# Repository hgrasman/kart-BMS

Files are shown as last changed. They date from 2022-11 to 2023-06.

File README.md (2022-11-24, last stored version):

# BMS

## Getting started

To make it easy for you to get started with GitLab, here's a list of recommended next steps.

Already a pro? Just edit this README.md and make it your own. Want to make it easy? [Use the template at the bottom](#editing-this-readme)!

## Add your files

- [ ] [Create](https://docs.gitlab.com/ee/user/project/repository/web_editor.html#create-a-file) or [upload](https://docs.gitlab.com/ee/user/project/repository/web_editor.html#upload-a-file) files
- [ ] [Add files using the command line](https://docs.gitlab.com/ee/gitlab-basics/add-file.html#add-a-file-using-the-command-line) or push an existing Git repository with the following command:

```
cd existing_repo
git remote add origin https://gitlab.com/ev-kartz/hardware/bms.git
git branch -M main
git push -uf origin main
```

## Integrate with your tools

- [ ] [Set up project integrations](https://gitlab.com/ev-kartz/hardware/bms/-/settings/integrations)

## Collaborate with your team

- [ ] [Invite team members and collaborators](https://docs.gitlab.com/ee/user/project/members/)
- [ ] [Create a new merge request](https://docs.gitlab.com/ee/user/project/merge_requests/creating_merge_requests.html)
- [ ] [Automatically close issues from merge requests](https://docs.gitlab.com/ee/user/project/issues/managing_issues.html#closing-issues-automatically)
- [ ] [Enable merge request approvals](https://docs.gitlab.com/ee/user/project/merge_requests/approvals/)
- [ ] [Automatically merge when pipeline succeeds](https://docs.gitlab.com/ee/user/project/merge_requests/merge_when_pipeline_succeeds.html)

## Test and Deploy

Use the built-in continuous integration in GitLab.

- [ ] [Get started with GitLab CI/CD](https://docs.gitlab.com/ee/ci/quick_start/index.html)
- [ ] [Analyze your code for known vulnerabilities with Static Application Security Testing(SAST)](https://docs.gitlab.com/ee/user/application_security/sast/)
- [ ] [Deploy to Kubernetes, Amazon EC2, or Amazon ECS using Auto Deploy](https://docs.gitlab.com/ee/topics/autodevops/requirements.html)
- [ ] [Use pull-based deployments for improved Kubernetes management](https://docs.gitlab.com/ee/user/clusters/agent/)
- [ ] [Set up protected environments](https://docs.gitlab.com/ee/ci/environments/protected_environments.html)

***

# Editing this README

When you're ready to make this README your own, just edit this file and use the handy template below (or feel free to structure it however you want - this is just a starting point!). Thank you to [makeareadme.com](https://www.makeareadme.com/) for this template.

## Suggestions for a good README
Every project is different, so consider which of these sections apply to yours. The sections used in the template are suggestions for most open source projects. Also keep in mind that while a README can be too long and detailed, too long is better than too short. If you think your README is too long, consider utilizing another form of documentation rather than cutting out information.

## Name
Choose a self-explaining name for your project.

## Description
Let people know what your project can do specifically. Provide context and add a link to any reference visitors might be unfamiliar with. A list of Features or a Background subsection can also be added here. If there are alternatives to your project, this is a good place to list differentiating factors.

## Badges
On some READMEs, you may see small images that convey metadata, such as whether or not all the tests are passing for the project. You can use Shields to add some to your README. Many services also have instructions for adding a badge.

## Visuals
Depending on what you are making, it can be a good idea to include screenshots or even a video (you'll frequently see GIFs rather than actual videos). Tools like ttygif can help, but check out Asciinema for a more sophisticated method.

## Installation
Within a particular ecosystem, there may be a common way of installing things, such as using Yarn, NuGet, or Homebrew. However, consider the possibility that whoever is reading your README is a novice and would like more guidance. Listing specific steps helps remove ambiguity and gets people to using your project as quickly as possible. If it only runs in a specific context like a particular programming language version or operating system or has dependencies that have to be installed manually, also add a Requirements subsection.

## Usage
Use examples liberally, and show the expected output if you can. It's helpful to have inline the smallest example of usage that you can demonstrate, while providing links to more sophisticated examples if they are too long to reasonably include in the README.

## Support
Tell people where they can go to for help. It can be any combination of an issue tracker, a chat room, an email address, etc.

## Roadmap
If you have ideas for releases in the future, it is a good idea to list them in the README.

## Contributing
State if you are open to contributions and what your requirements are for accepting them.

For people who want to make changes to your project, it's helpful to have some documentation on how to get started. Perhaps there is a script that they should run or some environment variables that they need to set. Make these steps explicit. These instructions could also be useful to your future self.

You can also document commands to lint the code or run tests. These steps help to ensure high code quality and reduce the likelihood that the changes inadvertently break something. Having instructions for running tests is especially helpful if it requires external setup, such as starting a Selenium server for testing in a browser.

## Authors and acknowledgment
Show your appreciation to those who have contributed to the project.

## License
For open source projects, say how it is licensed.

## Project status
If you have run out of energy or time for your project, put a note at the top of the README saying that development has slowed down or stopped completely. Someone may choose to fork your project or volunteer to step in as a maintainer or owner, allowing your project to keep going. You can also make an explicit request for maintainers.

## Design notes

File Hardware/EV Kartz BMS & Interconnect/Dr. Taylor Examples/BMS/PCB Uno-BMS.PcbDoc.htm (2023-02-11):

Reporting Options

# File in Previous Format

Date | : | 12/1/2022
Time | : | 7:33:51 PM
Filename | : | C:\Users\Public\Documents\Altium\Projects\EV Kartz BMS & Interconnect\Dr. Taylor Examples\BMS\PCB Uno-BMS.PcbDoc

Version | Warning
Release 12 | CAUTION - Air Gap Width previously controlled by Clearance rule is now controlled by Polygon Connect Style rule's newly introduced Air Gap Width (set to default value). Suggest reviewing each Polygon Connect Style rule's Air Gap Width attribute for correctness.
Release 13 | CAUTION - Silkscreen Over Component Pads Rules are converted to Silk To Solder Mask Clearance Rules. Suggest examining rule scopes for accuracy.

This file was generated by an earlier version of the software

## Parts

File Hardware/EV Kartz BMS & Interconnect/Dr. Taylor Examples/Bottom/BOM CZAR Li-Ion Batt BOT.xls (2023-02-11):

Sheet: BOM Report
Bill of Materials |  |  | Bill of Materials For Project [CZAR Li-Ion Batt BOT.PrjPcb] (No PCB Document Selected)
Source Data From: |  | CZAR Li-Ion Batt BOT.PrjPcb |  |  |  | Creation Date: | 11/23/2022 | 6:29:14 PM
Project: |  | CZAR Li-Ion Batt BOT.PrjPcb |  |  |  | Print Date: | 2022-11-23 | 18:30:44
Variant: |  | None |  |  |  | Author: | <Parameter Author not found> |  |  |  | Production Quantity: |  | 2
Designator | #Column Name Error:Value | Footprint | Comment | #Column Name Error:Rated | #Column Name Error:Tol | Description | Supplier 1 | Supplier Part Number 1 | Supplier Unit Price 1 | Quantity | Per Unit | Supplier Order Qty 1 | Supplier Subtotal 1 | Category | 1 | 5 | 10 | 25 | 50 | 100 | 250 | 500 | 1000
JH11, JH12, JH13, JH14, JH15, JH16, JH17, JH18, JH31, JH32, JH33, JH34, JH35, JH36, JH37, JH38, JH51, JH52, JH53, JH54, JH55, JH56, JH57, JH58, JH71, JH72, JH73, JH74, JH75, JH76, JH77, JH78, JH91, JH92, JH93, JH94, JH95, JH96, JH97, JH98, JHB1, JHB2, JHB3, JHB4, JHB5, JHB6, JHB7, JHB8, JL21, JL22, JL23, JL24, JL25, JL26, JL27, JL28, JL41, JL42, JL43, JL44, JL45, JL46, JL47, JL48, JL61, JL62, JL63, JL64, JL65, JL66, JL67, JL68, JL81, JL82, JL83, JL84, JL85, JL86, JL87, JL88, JLA1, JLA2, JLA3, JLA4, JLA5, JLA6, JLA7, JLA8, JLC1, JLC2, JLC3, JLC4, JLC5, JLC6, JLC7, JLC8 |  | BAT-KS5202-PTH | 5202 |  |  | Hardware, Battery Contact Spring, PCB-mount | Digi-Key | 36-5202-ND | $0.28 | 96 | $26.52 | 192 | 53.05 | J | 0.32000 | 0.32000 | 0.32000 | 0.28240 | 0.28240 | 0.27630 | 0.25920 | 0.23070 | 0.23070
J1, J2, J3, J4, J5, J6, J7, J8 |  | JST-XH-B6 | B6B-XH-A(LF)(SN) |  |  | Header, JST, 6-Pin, Straight | Digi-Key | 455-2271-ND | $0.24 | 8 | $1.90 | 16 | 3.81 | J | 0.28000 | 0.28000 | 0.23800 | 0.23800 | 0.23800 | 0.18530 | 0.18530 | 0.15882 | 0.15882
 |  |  |  |  |  |  |  |  |  | 104 | $28.43 | 208 | 56.86
Approved |  | Notes
Capacitor Cost: | $0.000 | C
Diode Cost: | $0.000 | D
Fuse Cost: | $0.000 | F
Hardware Cost: | $0.000 | H
Connector Cost: | $28.429 | J
Inductor Cost: | $0.000 | L
MOSFET Cost: | $0.000 | M
Transistor Cost: | $0.000 | Q
Resistor Cost: | $0.000 | R
Transformer Cost: | $0.000 | T
ASIC Cost: | $0.000 | U

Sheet: Project Information
Project Full Path | D:\Dropbox\!Projects\CZAR Power\Li-Ion Batt\BotBrd\CZAR Li-Ion Batt BOT.PrjPcb
Project Filename | CZAR Li-Ion Batt BOT.PrjPcb
Variant Name | None
Data-Source Filename | CZAR Li-Ion Batt BOT.PrjPcb
Data-Source Full Path | D:\Dropbox\!Projects\CZAR Power\Li-Ion Batt\BotBrd\CZAR Li-Ion Batt BOT.PrjPcb
Title | Bill of Materials For Project [CZAR Li-Ion Batt BOT.PrjPcb] (No PCB Document Selected)
Total Quantity | 104
Report Time | 6:29:14 PM
Report Date | 11/23/2022
Report Date & Tine | 11/23/2022 6:29:14 PM
Output Name | Bill of Materials
Output Type | BOM_PartType
Output Generator Name | BOM
Output Generator Description | Bill of Materials

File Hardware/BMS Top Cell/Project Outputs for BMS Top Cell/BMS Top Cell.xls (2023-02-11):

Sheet: BOM Report
Bill of Materials |  |  | Bill of Materials for PCB Document [Top_Cell.PcbDoc]
Source Data From: |  | Top_Cell.PcbDoc |  |  |  | Creation Date: | 2/11/2023 | 14:45
Project: |  | BMS Top Cell.PrjPcb |  |  |  | Print Date: | 2023-02-11 | 14:45:48
Variant: |  | None |  |  |  | Author: | <Parameter Author not found> |  |  |  | Production Quantity: |  | 1
Designator | Value | Footprint | Comment | Rated | Tol | Description | Supplier 1 | Supplier Part Number 1 | Supplier Unit Price 1 | Quantity | Per Unit | Supplier Order Qty 1 | Supplier Subtotal 1 | Category
C100, C101, C102, C103 | 10µF | CAPC3225N | C1210C106K3RACAUTO | 25V | 10% | Capacitor, Ceramic, 10µF, 25V, 0805, 10%, 125C | Digi-Key | 399-7046-1-ND | $0.65 | 4 | $2.60 | 4 | $2.60 | C
J1, J2, J3, J4, J5, J6, J7, J8, J9, J10, J11, J12, J13, J14, J15, J16, J17, J18, J19, J20, J21, J22 |  | 6mm Pad | 2036-3-57-15-00-00-03-0 |  |  | Hardware, Sprint Contact Surface | Digi-Key | 54-2036-3-57-15-00-00-03-0CT-ND | $0.78 | 22 | $17.07 | 22 | $17.07
J48V, JFUSE |  | S98979 | S98979 |  |  | Screw Terminal M8, 360A | Digi-Key | 2101-S98979-ND | $4.30 | 2 | $8.60 | 2 | $8.60
JIN, JOUT |  | JST-PH-S7 | S7B-PH-SM4-TB(LF)(SN) |  |  | Header, JST, 7-Pin, Right-Angle, PH, Surface Mount | Digi-Key | 455-1754-1-ND | $0.89 | 2 | $1.78 | 2 | $1.78 | J
R100, R101, R102, R103 | 100k | RESC2012N | ERJ-6ENF1003V | 1/8W | 1% | Resistor, Fixed, 100 kOhm, 0805, 1%, 1/8W | Digi-Key | P100KCCT-ND | $0.10 | 4 | $0.40 | 4 | $0.40 | R
R104, R105, R106, R107 | 10 | RESC2012N | ERJ-6ENF10R0V | 1/8W | 1% | Resistor, Fixed, 10 Ohm, 0805, 1%, 1/8W | Digi-Key | P10.0CCT-ND | $0.10 | 4 | $0.40 | 4 | $0.40 | R
 |  |  |  |  |  |  |  |  |  | 38 | $30.85 | 38 | $30.85
Approved |  | Notes
Capacitor Cost: | $2.600 | C
Diode Cost: | $0.000 | D
Fuse Cost: | $0.000 | F
Hardware Cost: | $0.000 | H
Connector Cost: | $1.780 | J
Inductor Cost: | $0.000 | L
MOSFET Cost: | $0.000 | M
Transistor Cost: | $0.000 | Q
Resistor Cost: | $0.800 | R
Transformer Cost: | $0.000 | T
ASIC Cost: | $0.000 | U

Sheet: Project Information
Project Full Path | C:\Users\pcguy\Desktop\GitLab\BMS\bms\Hardware\BMS Top Cell\BMS Top Cell.PrjPcb
Project Filename | BMS Top Cell.PrjPcb
Variant Name | None
Data-Source Filename | Top_Cell.PcbDoc
Data-Source Full Path | C:\Users\pcguy\Desktop\GitLab\BMS\bms\Hardware\BMS Top Cell\Top_Cell.PcbDoc
Title | Bill of Materials for PCB Document [Top_Cell.PcbDoc]
Total Quantity | 38
Report Time | 14:45
Report Date | 2/11/2023
Report Date & Tine | 2/11/2023 14:45
Output Name | Bill of Materials
Output Type | BomReport
Output Generator Name | BOM
Output Generator Description | Bill of Materials

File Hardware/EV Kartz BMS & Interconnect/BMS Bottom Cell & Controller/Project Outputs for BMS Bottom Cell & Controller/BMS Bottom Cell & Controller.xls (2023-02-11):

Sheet: BOM Report
Bill of Materials |  |  | Bill of Materials for PCB Document [Bottom_Cell.PcbDoc]
Source Data From: |  | Bottom_Cell.PcbDoc |  |  |  | Creation Date: | 2/11/2023 | 2:56 PM
Project: |  | BMS Bottom Cell & Controller.PrjPcb |  |  |  | Print Date: | 2023-02-11 | 14:56:14
Variant: |  | None |  |  |  | Author: | <Parameter Author not found> |  |  |  | Production Quantity: |  | 1
Designator | Value | Footprint | Comment | Rated | Tol | Description | Supplier 1 | Supplier Part Number 1 | Supplier Unit Price 1 | Quantity | Per Unit | Supplier Order Qty 1 | Supplier Subtotal 1 | Category
C100, C101, C104 | 1µF | CAPC2012N | C0805C105K3RAC7210 | 25V | 10% | Capacitor, Ceramic, 1µF, 25V, 0805, 10%, 125C | Digi-Key | 399-C0805C105K3RAC7210CT-ND | $0.13 | 3 | $0.39 | 3 | $0.39 | C
C102, C103, C105, C108, C109, C200, C201, C202, C203, C204, C205, C304, C307, C316 | 100nF | CAPC2012N | C0805C104K1RACAUTO | 100V | 10% | Capacitor, Ceramic, 100nF, 100V, 0805, 10%, 125C | Digi-Key | 399-6926-1-ND | $0.19 | 14 | $2.66 | 14 | $2.66 | C
C106, C107, C401 | 10µF | CAPC3225N | C1210C106K3RACAUTO | 25V | 10% | Capacitor, Ceramic, 10µF, 25V, 0805, 10%, 125C | Digi-Key | 399-7046-1-ND | $0.65 | 3 | $1.95 | 3 | $1.95 | C
C110, C309, C315, C400 | 10nF | CAPC2012N | C0805C103K1RAC7025 | 100V | 10% | Capacitor, Ceramic, 10nF, 100V, 0805, 10%, 125C | Digi-Key | 399-C0805C103K1RAC7025CT-ND | $0.10 | 4 | $0.40 | 4 | $0.40 | C
C300, C306 | 1 µF, [NoValue] | CAP 0805_2012 | =Value |  |  | CAP CER 1UF 100V X7S 0805 | Digi-Key | 490-14464-1-ND | $0.37 | 2 | $0.74 | 2 | $0.74
C301, C302, C303, C310, C312, C_ISO100 | 10 µF, [NoValue], 100 pF | CAP 1206_3216 - 0.8MM | =Value |  |  | CAP CER 10UF 25V X5R 1206, CAP CER 100PF 1KV C0G/NP0 1206 | Digi-Key | 1292-1206X106K250CT-ND, 1276-3199-1-ND | $0.49 | 6 | $2.94 | 6 | $2.94
C305, C308, C311, C313, C402, C404, C405 | 100nF | CAPC2012N | CL21B104KACNNNC | 100V | 10% | Capacitor, Ceramic, 100nF, 25V, 0805, 10%, 125C | Digi-Key | 1276-1099-1-ND | $0.10 | 7 | $0.70 | 7 | $0.70 | C
C314, C403, C406 | 1nF | CAPC2012N | C0805C102K1RACAUTO | 100V | 10% | Capacitor, Ceramic, 1nF, 100V, 0805, 10%, 125C | Digi-Key | 399-6919-1-ND | $0.19 | 3 | $0.57 | 3 | $0.57 | C
CAN100 |  | 618009211721 | 618009211721 |  |  | Male PCB Connector without Hex Screw WR-DSUB, 8.08 mm, Angled, 9 pins | Farnell | 2827767 | $3.06 | 1 | $3.06 | 1 | $3.06
D100 | GRN | DIO2012N-G | LTST-C170GKT | 2.1V, 10mA, 6mcd |  | LED, SMT 0805, Green, 2.1V, 10mA | Digi-Key | 160-1179-1-ND | $0.30 | 1 | $0.30 | 1 | $0.30 | D
D200 | RED | DIO2012N-R | LTST-C170KRKT | 2.0V, 20mA, 54mcd |  | LED, SMT 0805, Red, 2.0V, 20mA | Digi-Key | 160-1415-1-ND | $0.31 | 1 | $0.31 | 1 | $0.31 | D
D300, D301 |  | DIODES SOT-523 | =Part Number |  |  | DIODE ZENER 3.3V 150MW SOT523 | Digi-Key | MMBZ5226BTDICT-ND | $0.41 | 2 | $0.82 | 2 | $0.82
D400, D401 | 850mV @ 2A | SOD123 | SMD210PL-TP | 2A, 100V |  | Diode, Si Sch, 100V, 2A, SOD123 | Digi-Key | SMD210PL-TPMSCT-ND | $0.40 | 2 | $0.80 | 2 | $0.80 | D
F400 | 12mOhm | CAPC1608N | 0440005.WR | 5A, 32V |  | Fuse, SMT, 5A, 32VAC/VDC, 1206 | Digi-Key | F1608CT-ND | $1.09 | 1 | $1.09 | 1 | $1.09 | F
IC400, IC401 |  | DIODES SOT-23-3 | =Part Number |  |  | MOSFET N-CH 30V 4A SOT23 | Digi-Key | DMG3418L-7DICT-ND | $0.43 | 2 | $0.86 | 2 | $0.86
J200, J201, J202, J203, J204, J205, J206, J207, J208, J209, J210, J211, J212, J213, J214, J215, J216, J217, J218, J219, J220, J221 |  | 6mm Pad | 2036-3-57-15-00-00-03-0 |  |  | Hardware, Sprint Contact Surface | Digi-Key | 54-2036-3-57-15-00-00-03-0CT-ND | $0.78 | 22 | $17.07 | 22 | $17.07
J400, J_LEM300, J_Relay400 | 4 Pos | 22041041 | 22041041 | N/A | N/A | Header, 4 pos, 2.5mm pitch, Molex Kit Parts Housing: 0511910400 Terminals: 0508028000 | Digi-Key | WM18787-ND | $0.98 | 3 | $2.94 | 3 | $2.94 | J
JOUT400 |  | JST-PH-S7 | S7B-PH-SM4-TB(LF)(SN) |  |  | Header, JST, 7-Pin, Right-Angle, PH, Surface Mount | Digi-Key | 455-1754-1-ND | $0.89 | 1 | $0.89 | 1 | $0.89 | J
JPOS200 |  | S98979 | S98979 |  |  | Screw Terminal M8, 360A |  |  |  | 1 | $0.00
JPROG100 |  | HDR1X5 SMT | 3-647167-5 |  |  | Header, 1x5-Pin, SMT, 100mil Pitch | Digi-Key | A144616-ND | $3.28 | 1 | $3.28 | 1 | $3.28 | J
L100 | 220@100MHz | INDC2012N | 742792022 | 2A |  | Inductor, 220 Ohms @ 100MHz, 2A, 50 mOhm, Ferrite Bead | Digi-Key | 732-1614-1-ND | $0.23 | 1 | $0.23 | 1 | $0.23 | L
L101 | 10uH | INDC3225N | BRL3225T100K | 700mA, 0.42 Ohm |  | Inductor, 10uH, 700mA, 420mOhm, Ferrite Bead | Digi-Key | 587-2167-1-ND | $0.25 | 1 | $0.25 | 1 | $0.25 | L
M200 | 30mOhm @ 10V | TO252-3N | AOD454A | 40V, 20A |  | MOSFET, N-Ch, 40V, 20A, 430mOhm, TO252 | Digi-Key | 785-1223-1-ND | $0.67 | 1 | $0.67 | 1 | $0.67 | M
R100, R301, R302, R303, R305, R306, R308 | 120 Ohms, 604 kOhms, 200 Ohms, 52.3 kOhms, 150 kOhms | RES 0805_2012 | =Value |  |  | RES 120 OHM 1% 1/8W 0805, RES 604K OHM 1% 1/8W 0805, RES 200 OHM 0.5% 1/8W 0805, RES 52.3K OHM 1% 1/8W 0805, RES 150K OHM 0.1% 1/8W 0805 | Digi-Key | 311-120CRCT-ND, 738-RMCF0805FT604KCT-ND, P123819CT-ND, RMCF0805FT52K3CT-ND, P150KDACT-ND | $0.10 | 7 | $0.70 | 7 | $0.70
R101, R104, R204, R208, R304, R307, R311, R412, R413 | 10k | RESC2012N | ERJ-6ENF1002V | 1/8W | 1% | Resistor, Fixed, 10 kOhm, 0805, 1%, 1/8W | Digi-Key | P10.0KCCT-ND | $0.10 | 9 | $0.90 | 9 | $0.90 | R
R102, R103, R300, R309, R317 | 1k | RESC2012N | ERJ-6ENF1001V | 1/8W | 1% | Resistor, Fixed, 1 kOhm, 0805, 1%, 1/8W | Digi-Key | P1.00KCCT-ND | $0.10 | 5 | $0.50 | 5 | $0.50 | R
R200 | 499k | RESC2012N | ERJ-6ENF4993V | 1/8W | 1% | Resistor, Fixed, 499 kOhm, 0805, 1%, 1/8W | Digi-Key | P499KCCT-ND | $0.10 | 1 | $0.10 | 1 | $0.10 | R
R201, R203, R205, R206 | 1 | RESC6432N | 35221R0JT | 3W | 5% | Resistor, Power, 1 Ohm, 6432, 5%, 3W | Digi-Key | A121177CT-ND | $0.76 | 4 | $3.04 | 4 | $3.04 | R
R202, R_ISO100 | 1Meg | RESC2012N | ERJ-6ENF1004V | 1/8W | 1% | Resistor, Fixed, 1 MOhm, 0805, 1%, 1/8W | Digi-Key | P1.00MCCT-ND | $0.10 | 2 | $0.20 | 2 | $0.20 | R
R207, R402, R403, R406, R407, R410, R411 | 10 | RESC2012N | ERJ-6ENF10R0V | 1/8W | 1% | Resistor, Fixed, 10 Ohm, 0805, 1%, 1/8W | Digi-Key | P10.0CCT-ND | $0.10 | 7 | $0.70 | 7 | $0.70 | R
R209, R210, R211, R212, R213, R310, R400, R401, R404, R405, R408, R409 | 100k | RESC2012N | ERJ-6ENF1003V | 1/8W | 1% | Resistor, Fixed, 100 kOhm, 0805, 1%, 1/8W | Digi-Key | P100KCCT-ND | $0.09 | 12 | $1.10 | 12 | $1.10 | R
R214, R215, R216, R217, R218 | 100k | RESC2012N | NT08105F4050B1F | 3570K | 1% | Resistor, NTC Thermistor, 100kOhm, 0805, 1%, 125C | Digi-Key | 283-NT08105F4050B1FCT-ND | $0.29 | 5 | $1.45 | 5 | $1.45 | R
R312 | 100 | RESC2012N | ERJ-6ENF1000V | 1/8W | 1% | Resistor, Fixed, 100 Ohm, 0805, 1%, 1/8W | Digi-Key | P100CCT-ND | $0.10 | 1 | $0.10 | 1 | $0.10 | R
R313, R314, R315 | 30k | RESC2012N | ERJ-6ENF3002V | 1/8W | 1% | Resistor, Fixed, 30 kOhm, 0805, 1%, 1/8W | Digi-Key | P30.0KCCT-ND | $0.10 | 3 | $0.30 | 3 | $0.30 | R
R316 | 20k | RESC2012N | ERJ-6ENF2002V | 1/8W | 1% | Resistor, Fixed, 20 kOhm, 0805, 1%, 1/8W | Digi-Key | P20.0KCCT-ND | $0.10 | 1 | $0.10 | 1 | $0.10 | R
U100 |  | DIODES INC SOT-89 | =Part Number |  |  | IC REG LINEAR 5V 150MA SOT89 | Digi-Key | AP7381-50Y-13DICT-ND | $0.38 | 1 | $0.38 | 1 | $0.38
U101 |  | SOIC-8-300 | ADM3050EBRIZ |  |  | IC, Transceiver, CAN FD, 0.5-6V, ISOLATED | Digi-Key | 505-ADM3050EBRIZ-ND | $6.01 | 1 | $6.01 | 1 | $6.01 | U
U102 |  | SAMC21 | ATSAMC21E18A-ANT |  |  | ARM Microcontrollers - MCU 32TQFP,105C TEMP, GREEN, 5V, 48MHZ | Mouser | 556-ATSAMC21E18A-ANT | $4.49 | 1 | $4.49 | 1 | $4.49
U300 |  | SOT23-5N | AZV331KTR-G1 | 2.2V~5.5V |  | Comparator, Single, Open-Drain, 84mA, 2.2V~5.5V | Digi-Key | AZV331KTR-G1DICT-ND | $0.45 | 1 | $0.45 | 1 | $0.45 | U
U301 |  | DHC | LTC3265HDHC#PBF |  |  | Supply, Bipolar Charge Pump, +/-15V | Mouser | 584-LTC3265HDHC#PBF | $12.48 | 1 | $12.48 | 1 | $12.48
U302, U_danger400, U_warn400 |  | TSSOP-8 | 74AHC2G00DP,125 | 5.5V, 24mA |  | Logic, NAND, Dual, Schmitt Trigger, TSSOP-8 | Digi-Key | 1727-6521-1-ND | $0.48 | 3 | $1.44 | 3 | $1.44 | U
U303 |  | TI SOT-23-5 DBV | =Part Number |  |  | IC OPAMP GP 1 CIRCUIT SOT23-5 | Digi-Key | LM321MFX/NOPBCT-ND | $0.64 | 1 | $0.64 | 1 | $0.64
U304 |  | SOT23-5N | LMV321SN3T1G | 2.7V~5.5V, 160mA |  | Op-Amp, Single, 1MHz, 1V/us, R2R, 2.7V~5.5V, 160mA | Digi-Key | LMV321SN3T1GOSCT-ND | $0.55 | 1 | $0.55 | 1 | $0.55 | U
U400 |  | SOT23-6N | SN74LVC1G11DBVR | 1.65 ~ 5.5V |  | Logic, AND, Single, 3-In, SOT23-6 | Digi-Key | 296-16810-1-ND | $0.41 | 1 | $0.41 | 1 | $0.41 | U
 |  |  |  |  |  |  |  |  |  | 151 | $78.96 | 150 | $78.96
Approved |  | Notes
Capacitor Cost: | $6.670 | C
Diode Cost: | $1.410 | D
Fuse Cost: | $1.090 | F
Hardware Cost: | $0.000 | H
Connector Cost: | $7.110 | J
Inductor Cost: | $0.480 | L
MOSFET Cost: | $0.670 | M
Transistor Cost: | $0.000 | Q
Resistor Cost: | $8.494 | R
Transformer Cost: | $0.000 | T
ASIC Cost: | $8.860 | U

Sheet: Project Information
Project Full Path | C:\Users\Jon\Dropbox\EV Kartz\EV Kartz BMS & Interconnect\BMS Bottom Cell & Controller\BMS Bottom Cell & Controller.PrjPcb
Project Filename | BMS Bottom Cell & Controller.PrjPcb
Variant Name | None
Data-Source Filename | Bottom_Cell.PcbDoc
Data-Source Full Path | C:\Users\Jon\Dropbox\EV Kartz\EV Kartz BMS & Interconnect\BMS Bottom Cell & Controller\Bottom_Cell.PcbDoc
Title | Bill of Materials for PCB Document [Bottom_Cell.PcbDoc]
Total Quantity | 151
Report Time | 2:56 PM
Report Date | 2/11/2023
Report Date & Tine | 2/11/2023 2:56 PM
Output Name | Bill of Materials
Output Type | BomReport
Output Generator Name | BOM
Output Generator Description | Bill of Materials

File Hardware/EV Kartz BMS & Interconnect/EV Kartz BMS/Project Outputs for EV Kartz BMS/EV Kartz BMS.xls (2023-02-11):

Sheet: BOM Report
Bill of Materials |  |  | Bill of Materials for PCB Document [reg_PCB.PcbDoc]
Source Data From: |  | reg_PCB.PcbDoc |  |  |  | Creation Date: | 2/11/2023 | 4:03 PM
Project: |  | EV Kartz BMS.PrjPcb |  |  |  | Print Date: | 2023-02-11 | 16:03:29
Variant: |  | None |  |  |  | Author: | <Parameter Author not found> |  |  |  | Production Quantity: |  | 1
Designator | Value | Footprint | Comment | Rated | Tol | Description | Supplier 1 | Supplier Part Number 1 | Supplier Unit Price 1 | Quantity | Per Unit | Supplier Order Qty 1 | Supplier Subtotal 1 | Category
C100, C101, C102, C103, C104 | 10µF | CAPC3225N | C1210C106K3RACAUTO | 25V | 10% | Capacitor, Ceramic, 10µF, 25V, 0805, 10%, 125C | Digi-Key | 399-7046-1-ND | $0.65 | 5 | $3.25 | 5 | $3.25 | C
C105, C106, C107, C108, C109, C110 | 100nF | CAPC2012N | C0805C104K1RACAUTO | 100V | 10% | Capacitor, Ceramic, 100nF, 100V, 0805, 10%, 125C | Digi-Key | 399-6926-1-ND | $0.28 | 6 | $1.68 | 6 | $1.68 | C
D100 | RED | DIO2012N-R | LTST-C170KRKT | 2.0V, 20mA, 54mcd |  | LED, SMT 0805, Red, 2.0V, 20mA | Digi-Key | 160-1415-1-ND | $0.31 | 1 | $0.31 | 1 | $0.31 | D
D101 | GRN | DIO2012N-G | LTST-C170GKT | 2.1V, 10mA, 6mcd |  | LED, SMT 0805, Green, 2.1V, 10mA | Digi-Key | 160-1179-1-ND | $0.30 | 1 | $0.30 | 1 | $0.30 | D
F1 | 12mOhm | CAPC1608N | 0440005.WR | 5A, 32V |  | Fuse, SMT, 5A, 32VAC/VDC, 1206 | Digi-Key | F1608CT-ND | $1.09 | 1 | $1.09 | 1 | $1.09 | F
J200_N, J200_P, J201_N, J201_P, J202_N, J202_P, J203_N, J203_P, J204_N, J204_P, J205_N, J205_P, J206_N, J206_P, J207_N, J207_P, J208_N, J208_P, J209_N, J209_P, J210_N, J210_P, J211_N, J211_P, J212_N, J212_P, J213_N, J213_P, J214_N, J214_P, J215_N, J215_P, J216_N, J216_P, J217_N, J217_P, J218_N, J218_P, J219_N, J219_P, J220_N, J220_P, J221_N, J221_P |  | 6mm Pad | 2036-3-57-15-00-00-03-0 |  |  | Hardware, Sprint Contact Surface | Digi-Key | 54-2036-3-57-15-00-00-03-0CT-ND | $0.74 | 44 | $32.75 | 44 | $32.75
JIN100, JOUT100 |  | JST-PH-S7 | S7B-PH-SM4-TB(LF)(SN) |  |  | Header, JST, 7-Pin, Right-Angle, PH, Surface Mount | Digi-Key | 455-1754-1-ND | $0.89 | 2 | $1.78 | 2 | $1.78 | J
JPROG100 |  | HDR1X5 SMT | 3-647167-5 |  |  | Header, 1x5-Pin, SMT, 100mil Pitch | Digi-Key | A144616-ND | $3.28 | 1 | $3.28 | 1 | $3.28 | J
M100 | 30mOhm @ 10V | TO252-3N | AOD454A | 40V, 20A |  | MOSFET, N-Ch, 40V, 20A, 430mOhm, TO252 | Digi-Key | 785-1223-1-ND | $0.67 | 1 | $0.67 | 1 | $0.67 | M
R100, R101, R102, R103, R108, R112, R113, R114, R115 | 100k | RESC2012N | ERJ-6ENF1003V | 1/8W | 1% | Resistor, Fixed, 100 kOhm, 0805, 1%, 1/8W | Digi-Key | P100KCCT-ND | $0.10 | 9 | $0.90 | 9 | $0.90 | R
R104, R105, R106, R107, R124 | 10 | RESC2012N | ERJ-6ENF10R0V | 1/8W | 1% | Resistor, Fixed, 10 Ohm, 0805, 1%, 1/8W | Digi-Key | P10.0CCT-ND | $0.10 | 5 | $0.50 | 5 | $0.50 | R
R109, R119, R120, R121, R122 | 100k | RESC2012N | NT08105F4050B1F | 3570K | 1% | Resistor, NTC Thermistor, 100kOhm, 0805, 1%, 125C | Digi-Key | 283-NT08105F4050B1FCT-ND | $0.29 | 5 | $1.45 | 5 | $1.45 | R
R110, R111, R118, R123 | 1 | RESC6432N | 35221R0JT | 3W | 5% | Resistor, Power, 1 Ohm, 6432, 5%, 3W | Digi-Key | A121177CT-ND | $0.76 | 4 | $3.04 | 4 | $3.04 | R
R116, R117, R127 | 10k | RESC2012N | ERJ-6ENF1002V | 1/8W | 1% | Resistor, Fixed, 10 kOhm, 0805, 1%, 1/8W | Digi-Key | P10.0KCCT-ND | $0.10 | 3 | $0.30 | 3 | $0.30 | R
R125 | 499k | RESC2012N | ERJ-6ENF4993V | 1/8W | 1% | Resistor, Fixed, 499 kOhm, 0805, 1%, 1/8W | Digi-Key | P499KCCT-ND | $0.10 | 1 | $0.10 | 1 | $0.10 | R
R126 | 1Meg | RESC2012N | ERJ-6ENF1004V | 1/8W | 1% | Resistor, Fixed, 1 MOhm, 0805, 1%, 1/8W | Digi-Key | P1.00MCCT-ND | $0.10 | 1 | $0.10 | 1 | $0.10 | R
U100 | 32MHz | SOIC-20-300 | PIC16F1508T-I/SO | 2.3V ~ 5.5V |  | MCU, 8-Bit, 5V, 32MHz, 20-Pin SOIC | Digi-Key | PIC16F1578-I/SS-ND | $1.37 | 1 | $1.37 | 1 | $1.37 | U
 |  |  |  |  |  |  |  |  |  | 91 | $52.87 | 91 | $52.87
Approved |  | Notes
Capacitor Cost: | $4.930 | C
Diode Cost: | $0.610 | D
Fuse Cost: | $1.090 | F
Hardware Cost: | $0.000 | H
Connector Cost: | $5.060 | J
Inductor Cost: | $0.000 | L
MOSFET Cost: | $0.670 | M
Transistor Cost: | $0.000 | Q
Resistor Cost: | $6.390 | R
Transformer Cost: | $0.000 | T
ASIC Cost: | $1.370 | U

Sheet: Project Information
Project Full Path | C:\Users\Jon\Dropbox\EV Kartz\EV Kartz BMS & Interconnect\EV Kartz BMS\EV Kartz BMS.PrjPcb
Project Filename | EV Kartz BMS.PrjPcb
Variant Name | None
Data-Source Filename | reg_PCB.PcbDoc
Data-Source Full Path | C:\Users\Jon\Dropbox\EV Kartz\EV Kartz BMS & Interconnect\EV Kartz BMS\reg_PCB.PcbDoc
Title | Bill of Materials for PCB Document [reg_PCB.PcbDoc]
Total Quantity | 91
Report Time | 4:03 PM
Report Date | 2/11/2023
Report Date & Tine | 2/11/2023 4:03 PM
Output Name | Bill of Materials
Output Type | BomReport
Output Generator Name | BOM
Output Generator Description | Bill of Materials

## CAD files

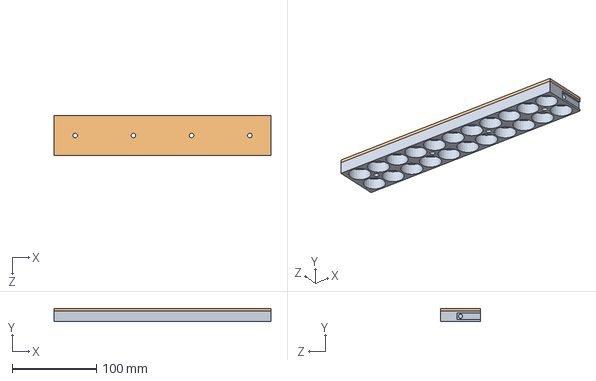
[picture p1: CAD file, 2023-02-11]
Hardware/EV Kartz BMS & Interconnect/EV Kartz BMS/Mechanical/21700_Battery_Pack_Dec20_2022/1_wide_cap_pcb_subassm.SLDASM
257.2 x 15.0 x 47.4 mm
Cap_21700_single
end_pcb

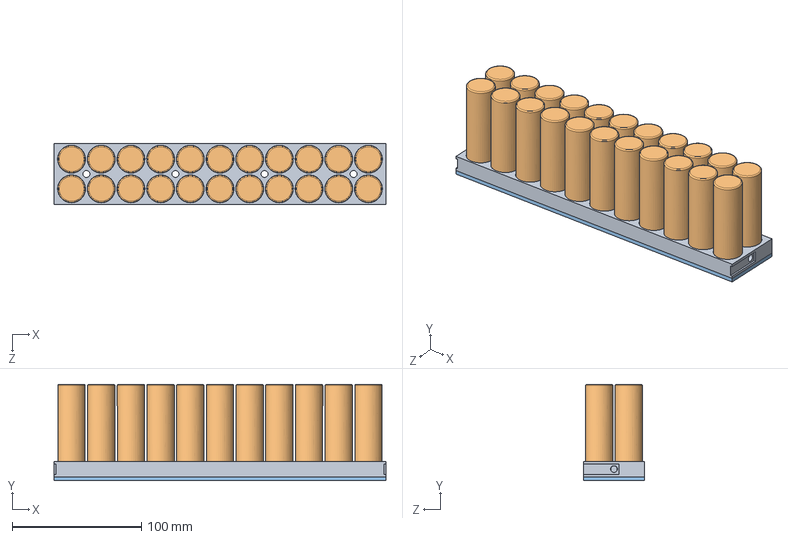
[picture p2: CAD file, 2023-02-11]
Hardware/EV Kartz BMS & Interconnect/EV Kartz BMS/Mechanical/21700_Battery_Pack_Dec20_2022/1_wide_subassm_neg.SLDASM
257.2 x 74.7 x 47.4 mm
Cap_21700_single
21700_Cell x 22
end_pcb

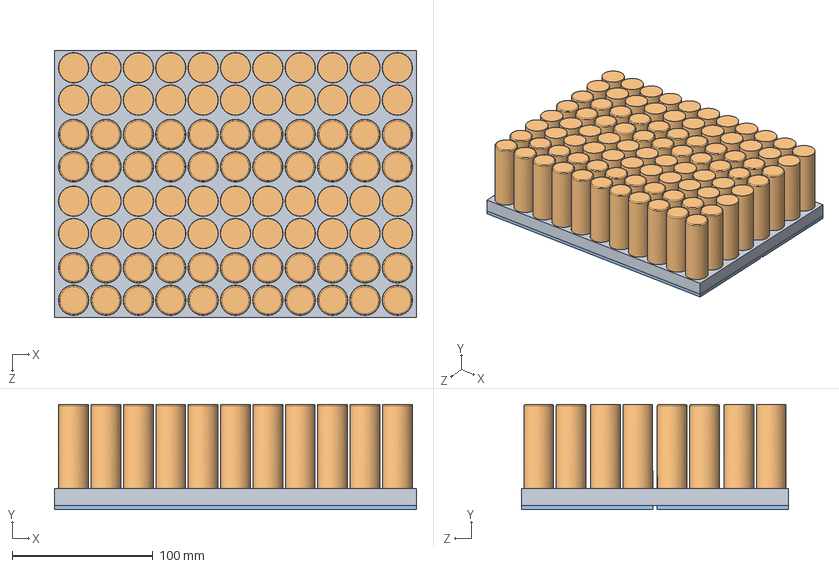
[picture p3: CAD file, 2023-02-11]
Hardware/EV Kartz BMS & Interconnect/EV Kartz BMS/Mechanical/21700_Battery_Pack_Dec20_2022/4_wide_subassm.SLDASM
257.2 x 74.7 x 189.6 mm
Cap_21700_double
21700_Cell x 88
4_wide_pcb x 2

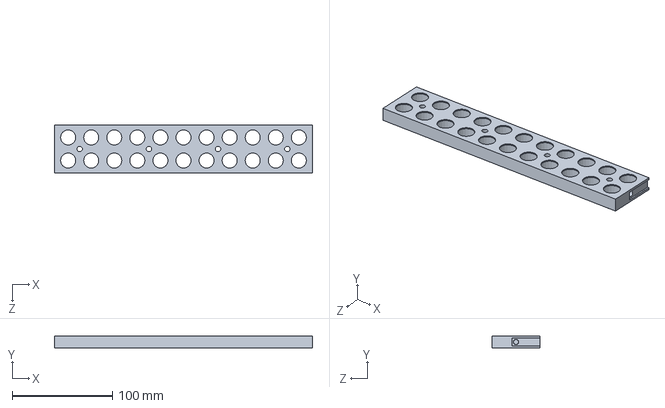
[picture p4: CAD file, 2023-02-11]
Hardware/EV Kartz BMS & Interconnect/EV Kartz BMS/Mechanical/21700_Battery_Pack_Dec20_2022/single_cap_w_pcb.SLDASM
257.2 x 12.0 x 47.4 mm

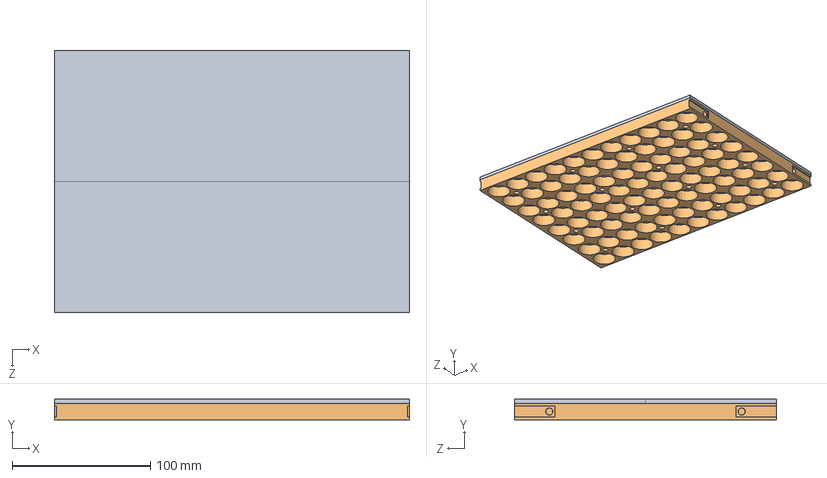
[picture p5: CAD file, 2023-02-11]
Hardware/EV Kartz BMS & Interconnect/EV Kartz BMS/Mechanical/21700_Battery_Pack_Dec20_2022/4_wide_cap_pcb_subassm.SLDASM
257.2 x 15.0 x 189.6 mm
4_wide_pcb x 2
Cap_21700_double

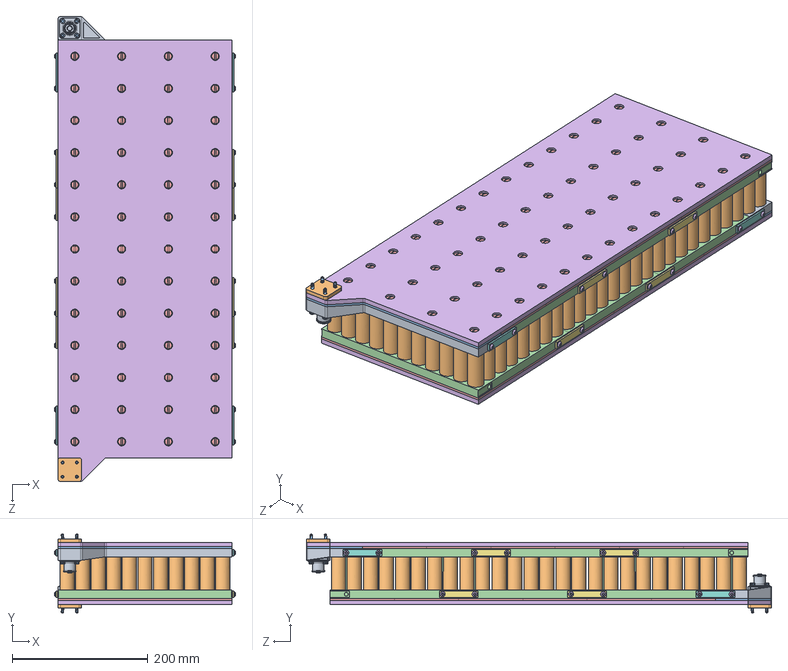
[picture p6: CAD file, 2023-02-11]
Hardware/EV Kartz BMS & Interconnect/EV Kartz BMS/Mechanical/21700_Battery_Pack_Dec20_2022/Assem_21700_Full_Pack.SLDASM
267.6 x 116.1 x 686.2 mm
Cap_21700_single x 2
21700_Cell x 286
end_pcb x 2
Cap_21700_double x 6
4_wide_pcb x 12
Clear_Cover x 2
Tie_Bar x 8
Tie_Bar_Short x 4
Surlok Plus 200A SLPRBTPSO x 2
91290A184_Black-Oxide Alloy Steel Socket Head Screw x 8
93121A375_6063_rod x 52
93121A375_6063_bolt x 52
92095A189_Button Head Hex Drive Screw x 24

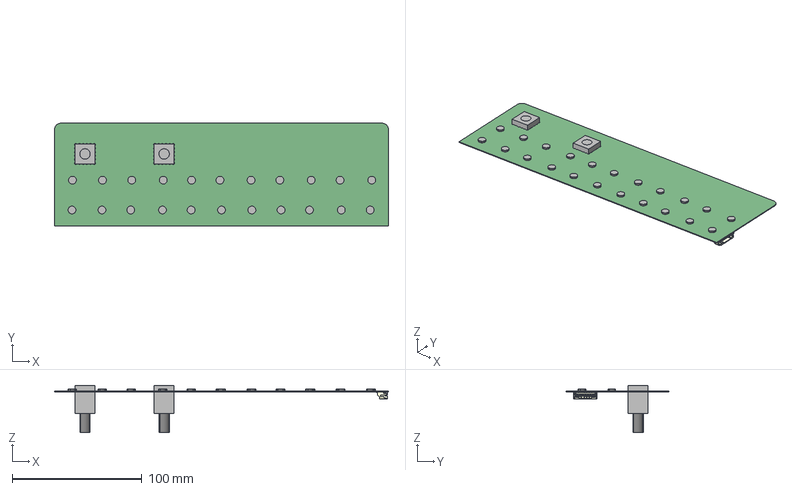
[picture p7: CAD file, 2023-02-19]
Hardware/BMS Top Cell/Project Outputs for BMS Top Cell/Top_Cell.step
257.2 x 79.1 x 36.5 mm
S7B-PH-SM4-TB-LF
Extruded x 26

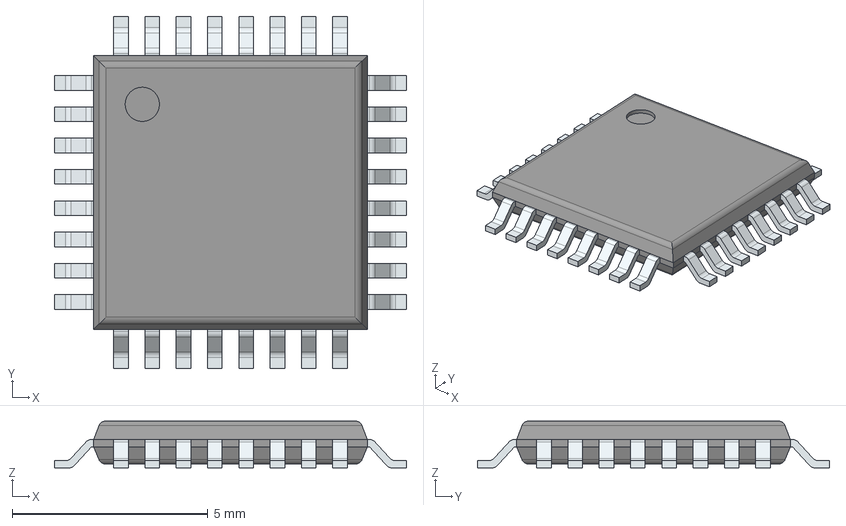
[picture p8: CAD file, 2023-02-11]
Hardware/EV Kartz BMS & Interconnect/BMS Bottom Cell & Controller/Mechanical/ATSAMC21E18A-ANT.stp
9.00 x 9.00 x 1.20 mm
PinsArrayLR
PinsArrayTB

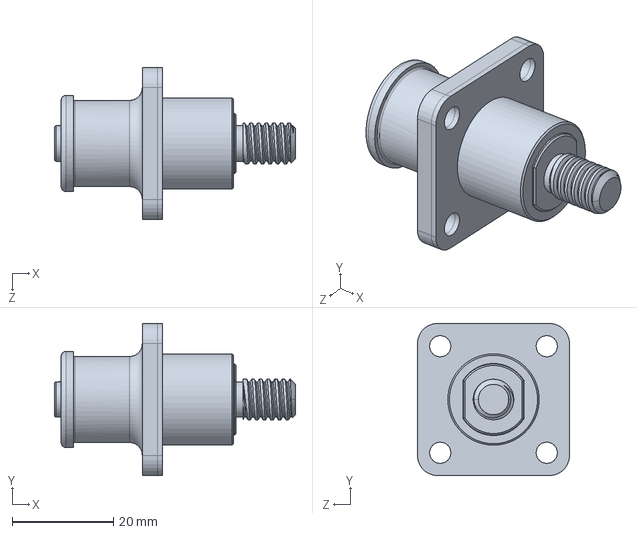
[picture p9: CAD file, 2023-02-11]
Hardware/EV Kartz BMS & Interconnect/EV Kartz BMS/Mechanical/21700_Battery_Pack_Dec20_2022/amphenol-surlok-plus-slprbtpso-1.snapshot.1/Surlok Plus 200A SLPRBTPSO.SLDPRT
47.5 x 30.0 x 30.0 mm

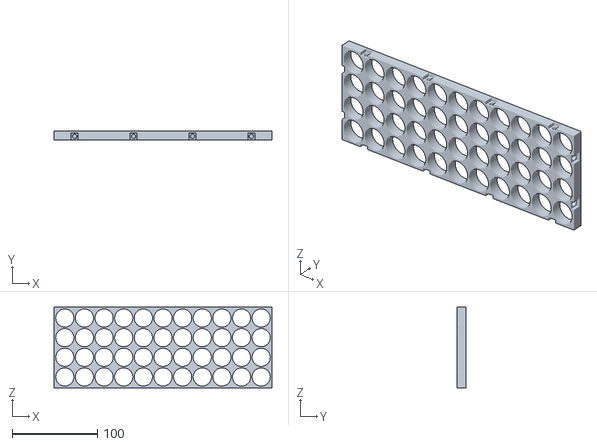
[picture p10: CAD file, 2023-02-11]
Hardware/EV Kartz BMS & Interconnect/EV Kartz BMS/Mechanical/21700_Battery_Pack_Dec20_2022/Test1/Cap_21700.STL
255.3 x 10.0 x 94.3

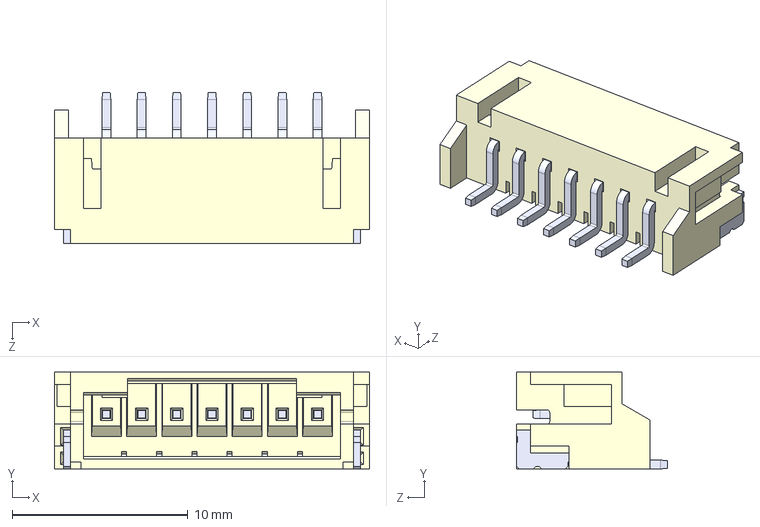
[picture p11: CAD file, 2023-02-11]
Hardware/EV Kartz BMS & Interconnect/EV Kartz BMS/Mechanical/S7B-PH-SM4-TB-LF.STEP
17.9 x 5.50 x 8.60 mm

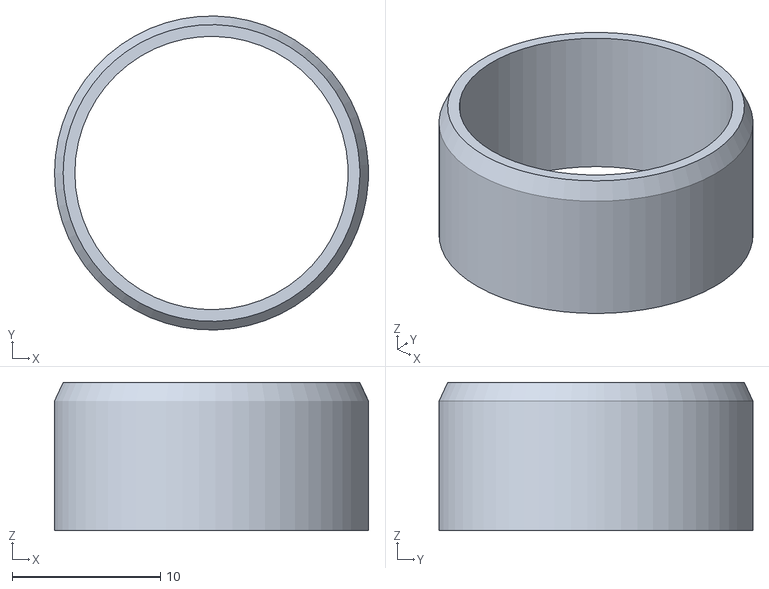
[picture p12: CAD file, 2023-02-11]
Hardware/EV Kartz BMS & Interconnect/EV Kartz BMS/Mechanical/21700_Battery_Pack_Dec20_2022/Test1/Spacer_Test1.STL
21.2 x 21.2 x 10.0

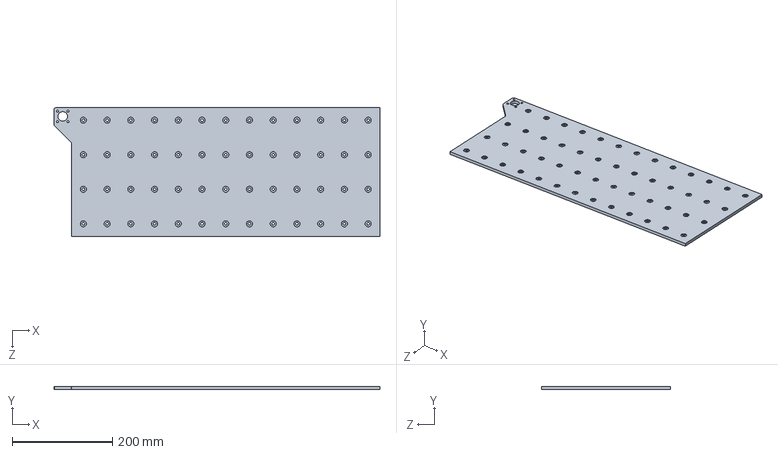
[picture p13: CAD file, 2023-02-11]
Hardware/EV Kartz BMS & Interconnect/EV Kartz BMS/Mechanical/21700_Battery_Pack_Dec20_2022/Clear_Cover.SLDPRT
651.2 x 6.35 x 257.2 mm

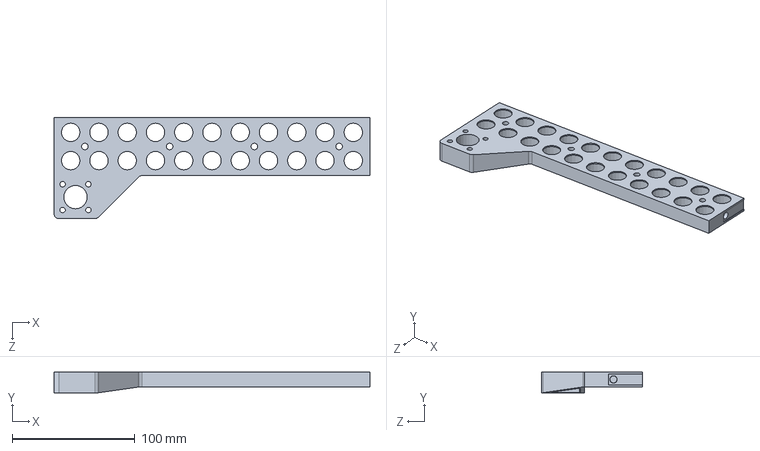
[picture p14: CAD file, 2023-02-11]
Hardware/EV Kartz BMS & Interconnect/EV Kartz BMS/Mechanical/21700_Battery_Pack_Dec20_2022/Cap_21700_single.SLDPRT
257.2 x 17.0 x 82.4 mm

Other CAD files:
Hardware/EV Kartz BMS & Interconnect/EV Kartz BMS/Mechanical/21700_Battery_Pack_Dec20_2022/1_wide_subassm_pos.SLDASM
Hardware/EV Kartz BMS & Interconnect/EV Kartz BMS/Mechanical/21700_Battery_Pack_Dec20_2022/1_wide_subassm.SLDASM
Hardware/EV Kartz BMS & Interconnect/EV Kartz BMS/Mechanical/21700_Battery_Pack_Dec20_2022/Cap_21700_single_a.SLDPRT
Hardware/EV Kartz BMS & Interconnect/EV Kartz BMS/Mechanical/21700_Battery_Pack_Dec20_2022/Tie_Bar.SLDPRT
Hardware/EV Kartz BMS & Interconnect/EV Kartz BMS/Mechanical/21700_Battery_Pack_Dec20_2022/21700_Cell.SLDPRT
Hardware/EV Kartz BMS & Interconnect/EV Kartz BMS/Mechanical/21700_Battery_Pack_Dec20_2022/21700_clearance_Test1.SLDPRT
Hardware/EV Kartz BMS & Interconnect/EV Kartz BMS/Mechanical/21700_Battery_Pack_Dec20_2022/4_wide_pcb.SLDPRT
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

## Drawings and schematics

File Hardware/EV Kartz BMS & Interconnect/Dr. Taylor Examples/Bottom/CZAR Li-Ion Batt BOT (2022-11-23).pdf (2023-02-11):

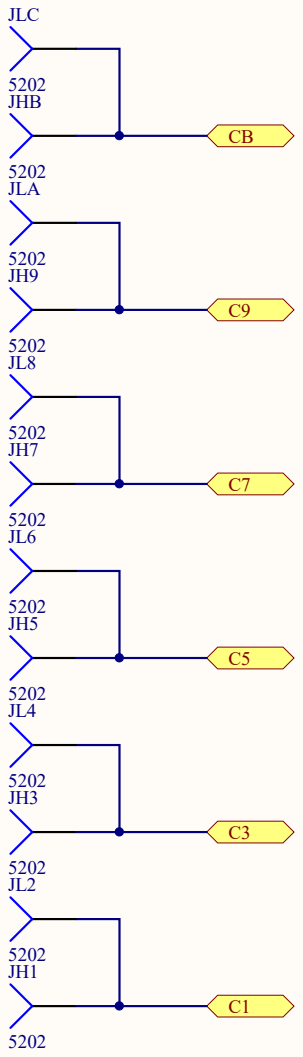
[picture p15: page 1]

CZAR Power - Li-Ion Batt Brd BOT Title | Adv Power Electronics Lab Kettering University 1700 University Ave Flint, MI 48504 United States of America

Size: Letter | Number: 2 | Revision:

Date: 11/23/2022 Time: 6:27:16 PM | | Sheet 2 of 7

D:\Dropbox\!Projects\CZAR Power\Li-Ion Batt\BotBrd\SCH Pg2 Cell Bank.SchDoc

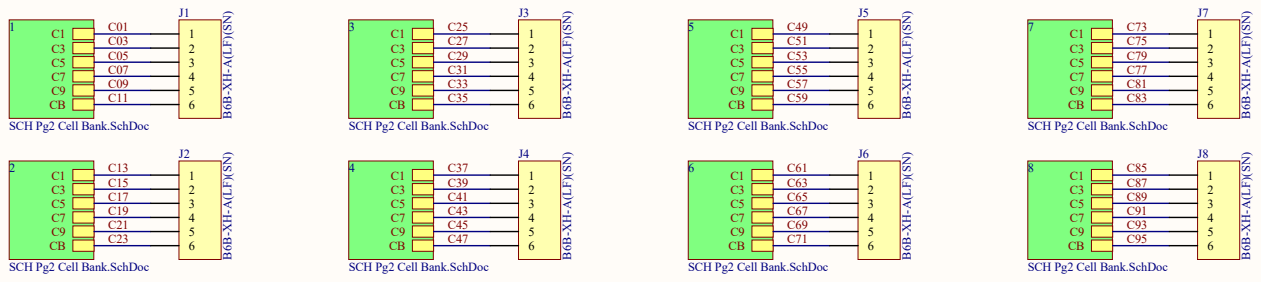
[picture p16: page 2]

CZA R Power - Li-Ion Batt Brd B O T | Adv Power Electronics Lab Kettering University 1700 University Av e Flint, MI 48504 United States of America

Letter | 2 | Re v ision:

11/23/2022 Time: 6:27:16 PM | | Sheet 2 of 7

AR Power\Li-Ion Batt\BotBrd\SCH Pg1 Top Sheet.SchDoc

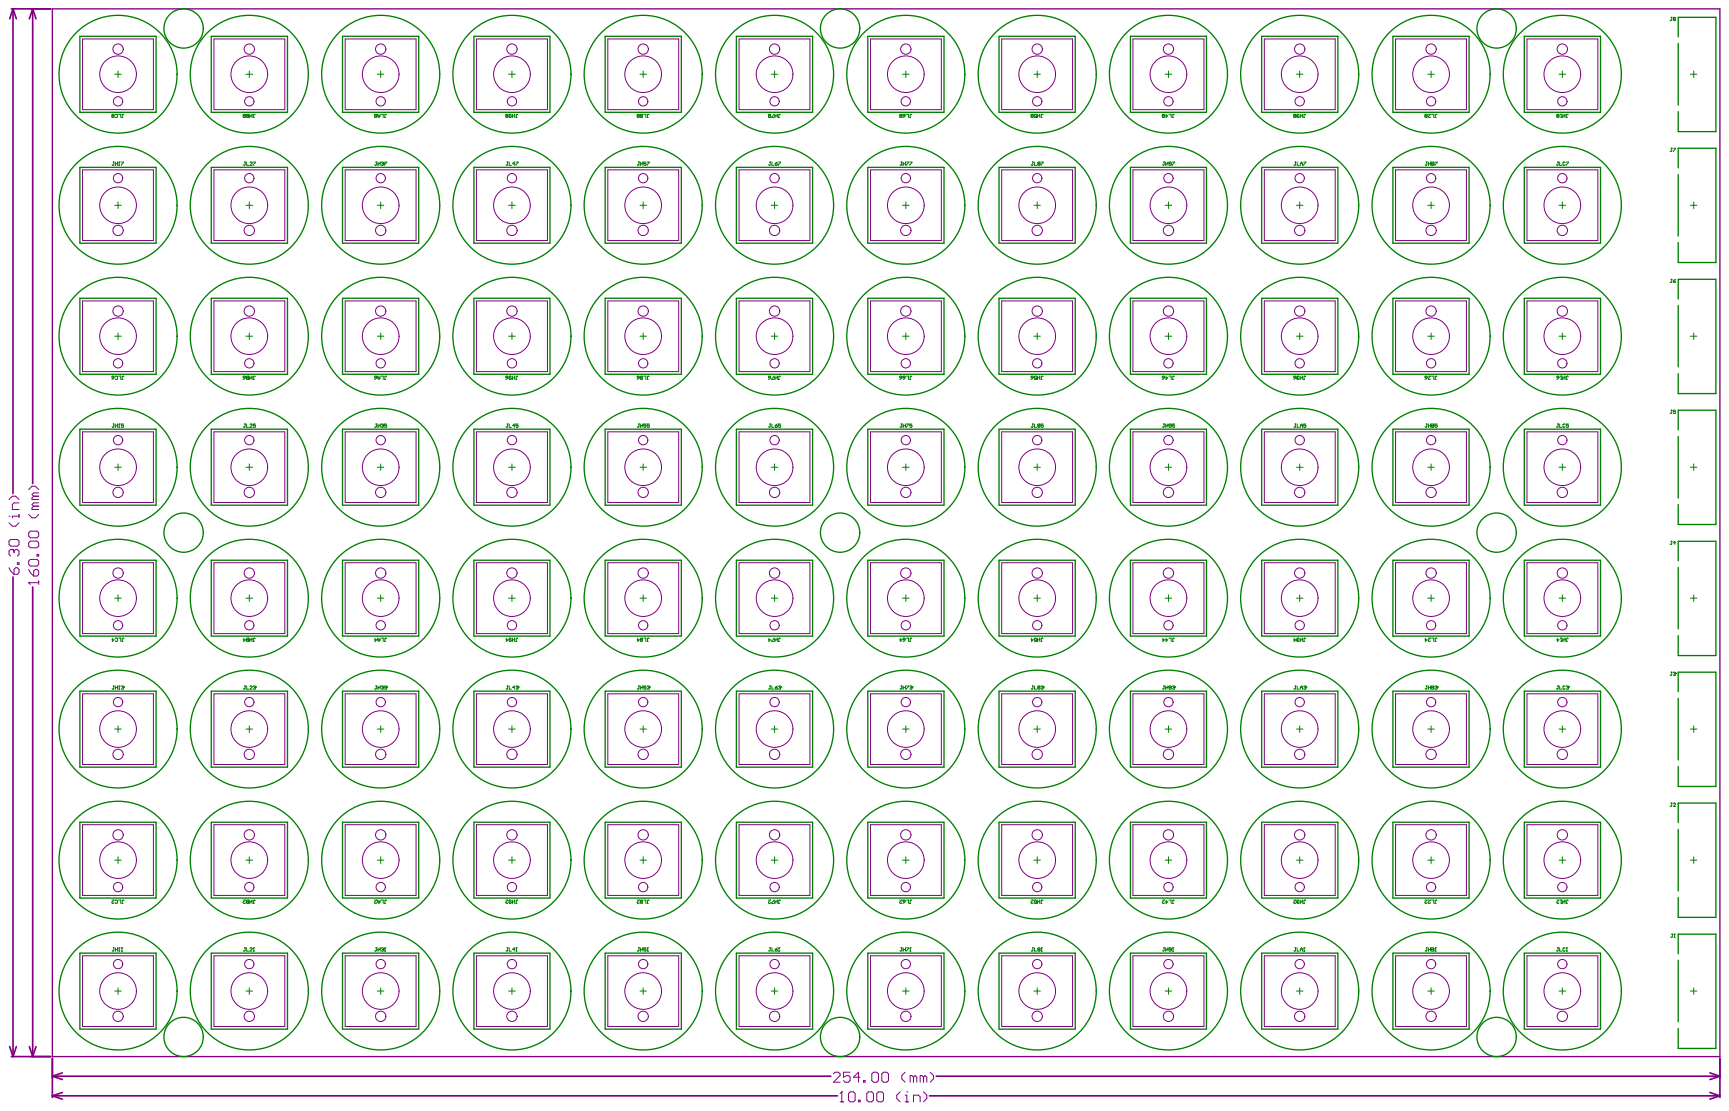
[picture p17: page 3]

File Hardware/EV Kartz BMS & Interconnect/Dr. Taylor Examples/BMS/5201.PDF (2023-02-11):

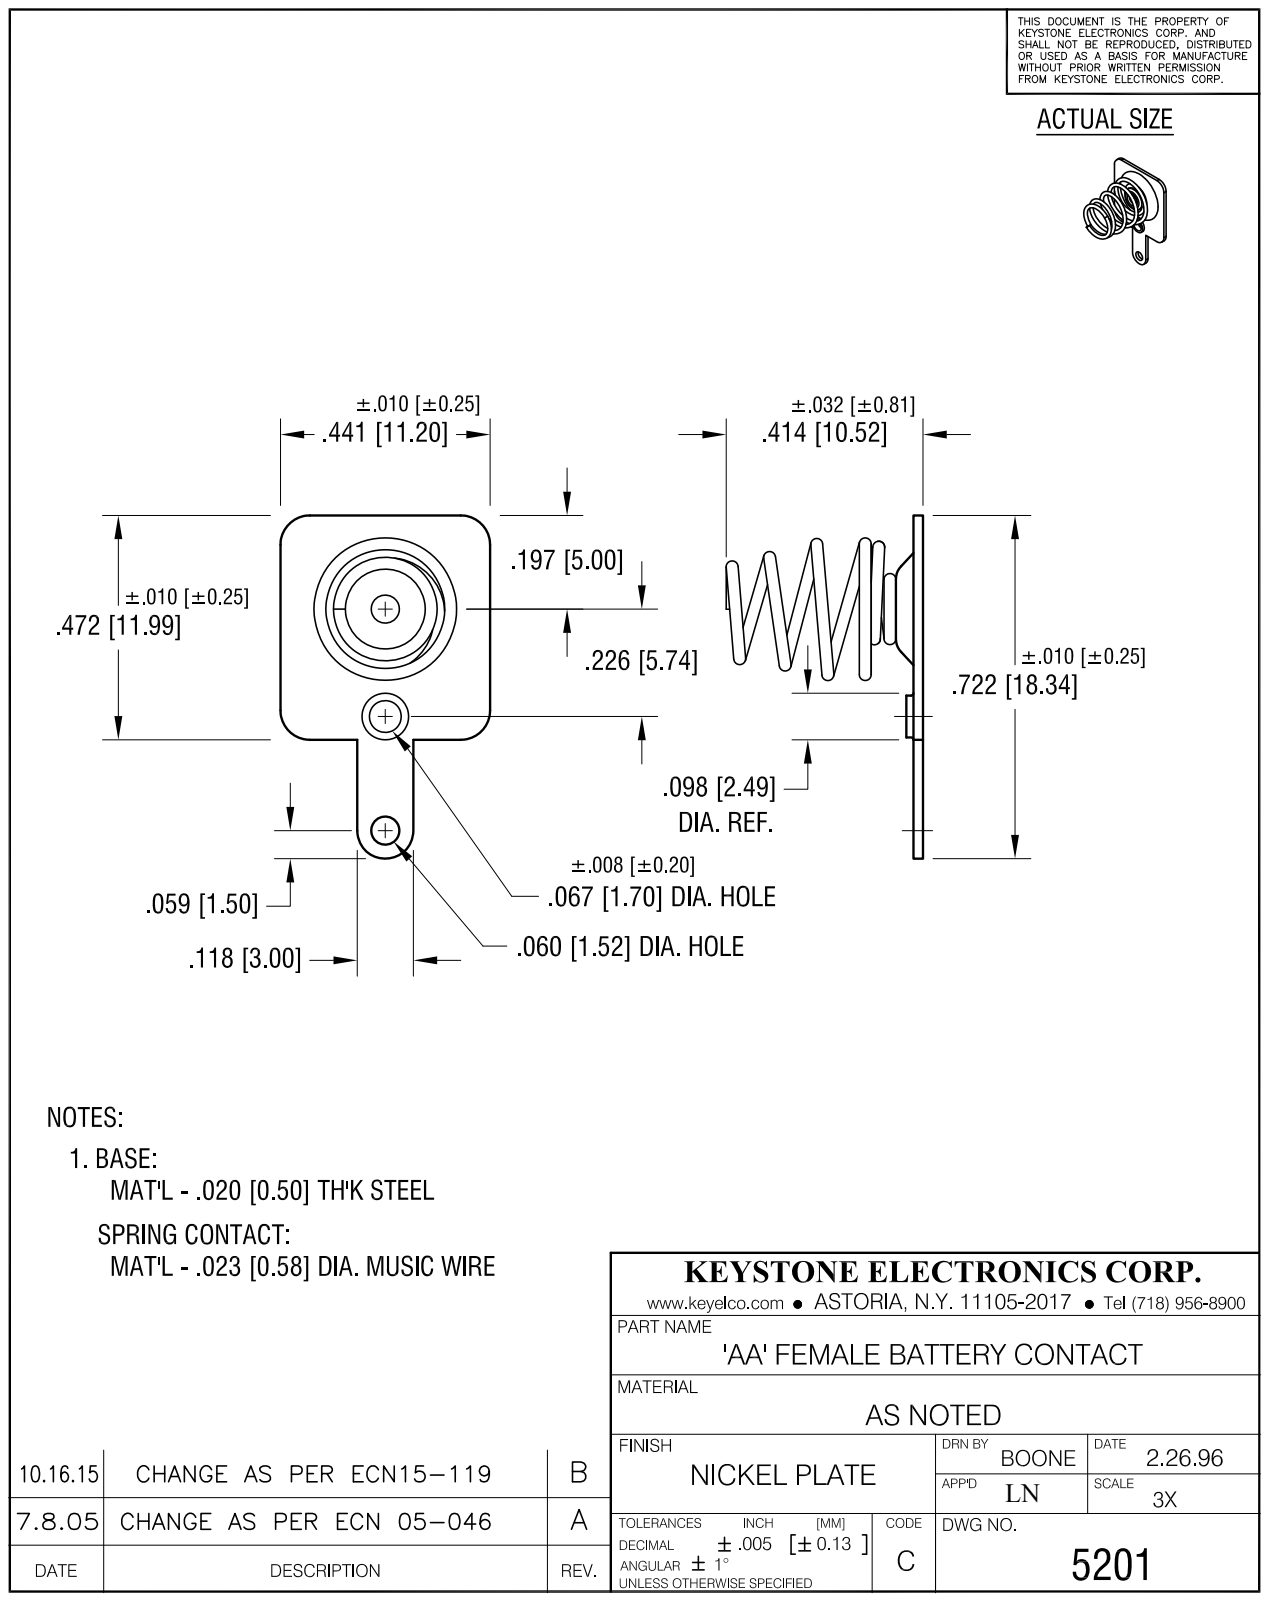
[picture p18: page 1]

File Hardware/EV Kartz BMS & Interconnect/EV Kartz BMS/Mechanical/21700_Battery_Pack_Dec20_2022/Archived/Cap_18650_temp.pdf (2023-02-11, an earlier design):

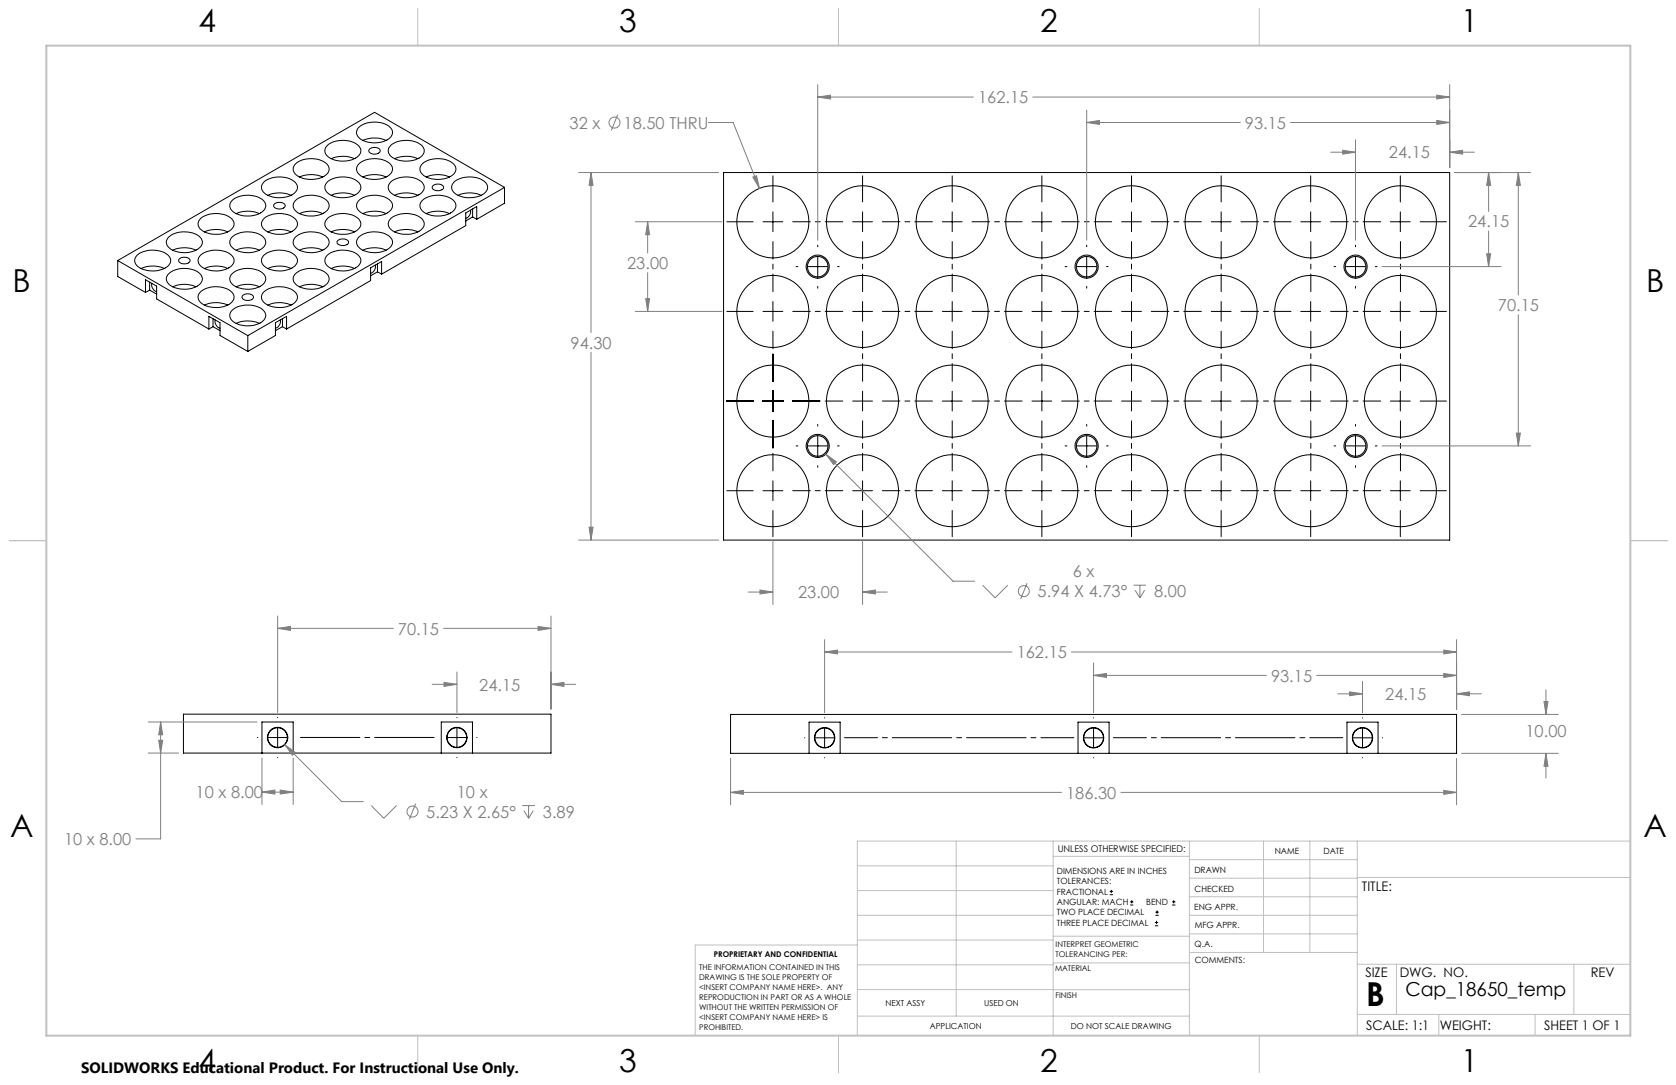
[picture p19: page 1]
32 x 18.50 THRU

UNLESS OTHERWISE SPECIFIED: | | NAME | DATE
DIMENSIONS ARE IN INCHES TOLERANCES: FRACTIONAL ANGULAR: MACH BEND TWO PLACE DECIMAL THREE PLACE DECIMAL | DRAWN

CHECKED | | | TITLE:

ENG APPR.
MFG APPR.

INTERPRET GEOMETRIC TOLERANCING PER: | Q.A.
MATERIAL | | SIZE B | DWG. NO. Cap_18650_temp | REV

PROPRIETARY AND CONFIDENTIAL
THE INFORMATION CONTAINED IN THIS
DRAWING IS THE SOLE PROPERTY OF
<INSERT COMPANY NAME HERE>. ANY
REPRODUCTION IN PART OR AS A WHOLE
WITHOUT THE WRITTEN PERMISSION OF
<INSERT COMPANY NAME HERE> IS
PROHIBITED.

NEXT ASSY | USED ON | FINISH

APPLICATION | DO NOT SCALE DRAWING | | SCALE: 1:1 | WEIGHT: | SHEET 1 OF 1

SOLIDWORKS Educational Product. For Instructional Use Only.

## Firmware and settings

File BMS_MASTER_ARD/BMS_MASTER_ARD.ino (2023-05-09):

#include <Wire.h>

#define SAM_VSENSE_PIN A5
#define SAM_BAL_PIN 5
#define SAM_T1_PIN A3
#define SAM_T2_PIN A4
#define SAM_RELAY_PIN 8
#define SAM_SSTART_PIN 10
#define SAM_CURR_PIN A2
#define SAM_CHARGE_SWITCH_PIN 7

inline void slowStartRelay(){ //  
  digitalWrite(SAM_SSTART_PIN, HIGH); //precharge for 4.5 seconds
  delay(900);
  digitalWrite(SAM_RELAY_PIN, HIGH); //close main relay
  delay(100);
  digitalWrite(SAM_SSTART_PIN, LOW); //disconnect precharge relay after additional .5s
}
inline void stopRelay(){ // 
  digitalWrite(SAM_RELAY_PIN, LOW); //cut relay
  digitalWrite(SAM_SSTART_PIN, LOW); //redundant just in case
}


unsigned long lastRead;
double current;
double charge = 0;

void setup() {

  // Setup I2C and uart
  Wire.begin();
  Serial.begin(115200);
  Wire.setWireTimeout(5000, true);

  //setup balance command 
  pinMode(SAM_BAL_PIN, OUTPUT);
  digitalWrite(SAM_BAL_PIN, LOW); //balance init off

  //setup Relay pins
  pinMode(SAM_RELAY_PIN, OUTPUT);
  pinMode(SAM_SSTART_PIN, OUTPUT);
  digitalWrite(SAM_RELAY_PIN, LOW);
  digitalWrite(SAM_SSTART_PIN, LOW);

  //setup charge/discharge switch pin
  pinMode(SAM_CHARGE_SWITCH_PIN, INPUT_PULLUP);
      
  lastRead = millis();
}

#define MINADDR 8
#define MAXADDR 19
#define CONTROLVOLT 0x11
#define ARRADDR addr-MINADDR
#define NUMTEMPS 5
#define BALANCETHRESH 0

#define CURRENT_MAX_ALLOWED 350 

#define MINV 3.2
#define MINV_LOADED 2.8
#define MAXV 4.2
#define MAXTEMP 60

#define LEM_CENTER_OFFSET 1.485
#define LEM_RANGE 3.0
#define CURRENTMAX 400

double avgs[MAXADDR - MINADDR + 1];
bool balnce[MAXADDR - MINADDR + 1];
double temps[MAXADDR - MINADDR + 1][NUMTEMPS];
bool sam_balance;
double sam_volt;
double sam_temp1;
double sam_temp2;
bool chargeMode;
bool relayClosed = false;

void loop() {
  // put your main code here, to run repeatedly:

  union booga{
    uint8_t raw[2];
    uint16_t mashed;
  }booling;  

  chargeMode = digitalRead(SAM_CHARGE_SWITCH_PIN); //poll switch for pack mode

  double rel_avg = 0;
  uint8_t count = 0;
  double min_v = 5;
  double max_v = 0;
  double max_temp = 0;
  for (int addr = MINADDR; addr <= MAXADDR; addr++ ){
    //Serial.print("Polling:"); Serial.println(addr);

    Wire.beginTransmission(addr);
    Wire.write(CONTROLVOLT | balnce[ARRADDR]<<5);
    byte error = Wire.endTransmission(); // run transaction
    delay(6);

    if (error){
      //Serial.println("NACK");
      avgs[ARRADDR] = -1;
    }else{
      Wire.requestFrom(addr, 2);
      booling.raw[0] = Wire.read();
      booling.raw[1] = Wire.read();
      if (avgs[ARRADDR]>0){ avgs[ARRADDR] = (double) (.85*(double)avgs[ARRADDR] + .15*(double)booling.mashed);} //convert to volts
      else{avgs[ARRADDR] = (double)booling.mashed;} //lost contact, get value
      double volts = (2.048 * 1024) / avgs[ARRADDR];
      Serial.print("Found: "); Serial.print(addr); Serial.print(" Counts: "); Serial.print(avgs[ARRADDR]); Serial.print(" VOLTS: "); Serial.println(volts);
      rel_avg += volts; count++;
      if (volts>max_v){max_v = volts;}
      if (volts<min_v){min_v = volts;}

      //get temp data
      for (int i = 0; i<NUMTEMPS; i++){
        Wire.beginTransmission(addr);
        Wire.write((uint8_t) i+1 | balnce[ARRADDR]<<5);
        byte error = Wire.endTransmission(); // run transaction
        delay(6);

        if (error){
          //Serial.println("NACK");
          temps[ARRADDR][i] = -1;
        }else{
          Wire.requestFrom(addr, 2);
          booling.raw[0] = Wire.read();
          booling.raw[1] = Wire.read();      
        }
        if (temps[ARRADDR][i]>0){ temps[ARRADDR][i] = (double) (.5*(double)temps[ARRADDR][i] + .5*(double)booling.mashed);} //convert to volts
        else{temps[ARRADDR][i] = (double)booling.mashed;} //lost contact, get value
        double temp_OHMS = -(100000*temps[ARRADDR][i]) / (temps[ARRADDR][i] - 1024);
        double temp_actual = 55.31 * exp((temp_OHMS/1000)*-0.07449) + 63.29*exp((temp_OHMS/1000)*-0.009305);
        if (temp_actual < 500){
          if (temp_actual>max_temp){max_temp = temp_actual;}
        }
        Serial.print(" T"); Serial.print(i+1); Serial.print(": "); Serial.print(temp_actual);
        delay(3);
      }   
      Serial.println();       
    }
    delay(3);  

  }

  digitalWrite(SAM_BAL_PIN, LOW); //stop balancing
  delay(80); //necessary for voltage to stabilize
  sam_volt = .5*sam_volt + .5*(double) analogRead(SAM_VSENSE_PIN); //include samc
  double sam_volt_actual = (sam_volt*5 ) / 1024;
  if (sam_volt_actual>max_v){max_v = sam_volt_actual;}
  if (sam_volt_actual<min_v){min_v = sam_volt_actual;}
  sam_temp1 = .5*sam_temp1 + .5*(double) analogRead(SAM_T1_PIN);
  sam_temp2 = .5*sam_temp2 + .5*(double) analogRead(SAM_T2_PIN);
  double sam_t1_OHMS = -(100000*sam_temp1) / (sam_temp1 - sam_volt); //scales temp reading to pack voltage
  double sam_t2_OHMS = -(100000*sam_temp2) / (sam_temp2 - sam_volt); //because thermistors are not referenced to 5v
  double sam_T1_actual = 55.31 * exp((sam_t1_OHMS/1000)*-0.07449) + 63.29*exp((sam_t1_OHMS/1000)*-0.009305);
  double sam_T2_actual = 55.31 * exp((sam_t2_OHMS/1000)*-0.07449) + 63.29*exp((sam_t2_OHMS/1000)*-0.009305);
  Serial.print("NEG: Volt: "); Serial.print(sam_volt_actual); Serial.print(" T1: "); Serial.print(sam_T1_actual); Serial.print(" T2: "); Serial.println(sam_T2_actual); 

  //calculate avg voltages
  if (count>1){
    rel_avg += sam_volt_actual; //include samc
    Serial.print("Count: "); Serial.print(count); Serial.print(" TOT: "); Serial.println(rel_avg);
    rel_avg = rel_avg/(count+1);
  }else if (count==1){
    rel_avg = rel_avg;
  }else{
    Serial.println("Zero Count");
    rel_avg = -1;
  }

  //decide balancing
  for (int addr = MINADDR; addr <= MAXADDR; addr++ ){
    if (avgs[ARRADDR]<0){continue;}   
    if (rel_avg<0){break;} 
    double volts = (2.048 * 1024) / avgs[ARRADDR];
    if (chargeMode && ((volts - rel_avg) > BALANCETHRESH)){ //flag for balance during charge only
      balnce[ARRADDR] = true;
      Serial.print("Balancing: "); Serial.println(addr);
    }else{
      balnce[ARRADDR] = false;
    }  
  }

  if (rel_avg>0){
    if (chargeMode && ((sam_volt_actual - rel_avg) > BALANCETHRESH)){
      digitalWrite(SAM_BAL_PIN, HIGH);
      Serial.println("Balancing SAM");
    }
  }

  Serial.print("MIN: "); Serial.print(min_v);  Serial.print(" AVG: "); Serial.print(rel_avg); Serial.print(" MAX: "); Serial.println(max_v);
  Serial.print("MAX TEMP: "); Serial.println(max_temp);

  //current sensing
  double lem_volts = ((double)analogRead(SAM_CURR_PIN)*5)/1024;
  current = (1 * ((double) ((lem_volts - LEM_CENTER_OFFSET)/(LEM_RANGE/2)) * CURRENTMAX)) + ((double) (7 + 7 * (lem_volts-LEM_CENTER_OFFSET))); //Current
  charge += current*(double)(lastRead-millis()) /1000; //charge count
  lastRead = millis();
  Serial.print("LEM Volts: "); Serial.print(lem_volts); Serial.print("Current: "); Serial.print(current); Serial.print(" Charge: "); Serial.println(charge);


  //determine if relay should be closed/open
  if (chargeMode && relayClosed){ 
    stopRelay(); //open relay
    relayClosed = false;
    Serial.println("RELAY OPEN: CHARGE READY");
  }
  if (!chargeMode && !relayClosed){ //need to discharge but relay is open
    if (min_v > MINV){ //close if above min cell voltage
      slowStartRelay(); //close relay
      relayClosed = true;
      Serial.println("RELAY CLOSED: DISCHARGE READY");
    }else{Serial.println("CANNOT CLOSE RELAY: VOLTAGE LOW");}
  }

  // enforce safety limits
  if (chargeMode){
    if (max_v >= MAXV){stopRelay(); relayClosed = false; Serial.println("RELAY TRIP MAX V");} //too high disconnect charger
  }else{
    if (min_v <= MINV_LOADED){stopRelay(); relayClosed = false; Serial.println("RELAY TRIP MIN V");} //enforce minimum loaded
  }
  if (current > CURRENT_MAX_ALLOWED){
    stopRelay();
    Serial.println("OVERCURRENT: TIMEOUT 1s");
    delay(1000);
  }
  if (max_temp>MAXTEMP){
    stopRelay();
    Serial.println("OVERTEMP: TIMEOUT 1s");
    delay(1000);
  }
  if (count == 0) {
    stopRelay();
    Serial.println("Cell Lost: TIMEOUT 1s");
    delay(1000);
  } 
  
}

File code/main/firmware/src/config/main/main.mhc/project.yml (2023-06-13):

files:
- generatedChecksum: E4894B6355AF41AED546E4C6C20005C1
  logicalPath: FreeRTOS/Source
  name: FreeRTOS_tasks.c
  physicalPath: ../../third_party/rtos/FreeRTOS/Source
  security: NON_SECURE
  type: SOURCE
  userChecksum: E4894B6355AF41AED546E4C6C20005C1
- generatedChecksum: null
  logicalPath: ''
  name: average.c
  physicalPath: ../..
  security: NON_SECURE
  type: SOURCE
  userChecksum: null
- generatedChecksum: null
  logicalPath: ''
  name: can.c
  physicalPath: ../..
  security: NON_SECURE
  type: SOURCE
  userChecksum: null
- generatedChecksum: null
  logicalPath: ''
  name: checks.c
  physicalPath: ../..
  security: NON_SECURE
  type: SOURCE
  userChecksum: null
- generatedChecksum: 4490B523D4D89767AF3FE31B825F7F6D
  logicalPath: FreeRTOS/Source
  name: croutine.c
  physicalPath: ../../third_party/rtos/FreeRTOS/Source
  security: NON_SECURE
  type: SOURCE
  userChecksum: 4490B523D4D89767AF3FE31B825F7F6D
- generatedChecksum: null
  logicalPath: ''
  name: current.c
  physicalPath: ../..
  security: NON_SECURE
  type: SOURCE
  userChecksum: null
- generatedChecksum: AE64199B660AA4499B58FCA9D9AD5792
  logicalPath: config/main/driver/i2c
  name: drv_i2c.c
  physicalPath: driver/i2c/src
  security: NON_SECURE
  type: SOURCE
  userChecksum: AE64199B660AA4499B58FCA9D9AD5792
- generatedChecksum: 37780F17759DED907A0F36E28BFB3136
  logicalPath: config/main/driver/i2c
  name: drv_i2c_local.h
  physicalPath: driver/i2c/src
  security: NON_SECURE
  type: SOURCE
  userChecksum: 37780F17759DED907A0F36E28BFB3136
- generatedChecksum: 0E0E8AECB67046FEA847B359ACE7A1F6
  logicalPath: FreeRTOS/Source
  name: event_groups.c
  physicalPath: ../../third_party/rtos/FreeRTOS/Source
  security: NON_SECURE
  type: SOURCE
  userChecksum: 0E0E8AECB67046FEA847B359ACE7A1F6
- generatedChecksum: 0D18A719A1E40A8875895284967F66D0
  logicalPath: config/main
  name: exceptions.c
  physicalPath: ''
  security: NON_SECURE
  type: SOURCE
  userChecksum: 0D18A719A1E40A8875895284967F66D0
- generatedChecksum: CF89BE92AE72229779903C2E9A760455
  logicalPath: config/main
  name: freertos_hooks.c
  physicalPath: ''
  security: NON_SECURE
  type: SOURCE
  userChecksum: CF89BE92AE72229779903C2E9A760455
- generatedChecksum: 4FDCB89CAB87567FDE8E7117FDDB2BBE
  logicalPath: FreeRTOS/Source/portable/MemMang
  name: heap_4.c
  physicalPath: ../../third_party/rtos/FreeRTOS/Source/portable/MemMang
  security: NON_SECURE
  type: SOURCE
  userChecksum: 4FDCB89CAB87567FDE8E7117FDDB2BBE
- generatedChecksum: null
  logicalPath: ''
  name: i2c.c
  physicalPath: ../..
  security: NON_SECURE
  type: SOURCE
  userChecksum: null
- generatedChecksum: 624232E70A9ECDE655E8B4F33F85CC02
  logicalPath: config/main
  name: initialization.c
  physicalPath: ''
  security: NON_SECURE
  type: SOURCE
  userChecksum: 624232E70A9ECDE655E8B4F33F85CC02
- generatedChecksum: 06C63C127F95F47D8B67A163B415CCE8
  logicalPath: config/main
  name: interrupts.c
  physicalPath: ''
  security: NON_SECURE
  type: SOURCE
  userChecksum: 06C63C127F95F47D8B67A163B415CCE8
- generatedChecksum: 2CDCA8CDF135BDEB85FDFC0A2A991C0B
  logicalPath: config/main
  name: libc_syscalls.c
  physicalPath: ''
  security: NON_SECURE
  type: SOURCE
  userChecksum: 2CDCA8CDF135BDEB85FDFC0A2A991C0B
- generatedChecksum: 47F98BAFD5D2A077AB529D10DB870AFF
  logicalPath: FreeRTOS/Source
  name: list.c
  physicalPath: ../../third_party/rtos/FreeRTOS/Source
  security: NON_SECURE
  type: SOURCE
  userChecksum: 47F98BAFD5D2A077AB529D10DB870AFF
- generatedChecksum: null
  logicalPath: ''
  name: main.c
  physicalPath: ../..
  security: NON_SECURE
  type: SOURCE
  userChecksum: null
- generatedChecksum: 8FDD6248506F28B32C4F5FD9AA0D9C6F
  logicalPath: config/main/osal
  name: osal_freertos.c
  physicalPath: osal
  security: NON_SECURE
  type: SOURCE
  userChecksum: 8FDD6248506F28B32C4F5FD9AA0D9C6F
- generatedChecksum: 79817893312FA69FAFCCBEB29D3E4891
  logicalPath: config/main/peripheral/adc
  name: plib_adc0.c
  physicalPath: peripheral/adc
  security: NON_SECURE
  type: SOURCE
  userChecksum: 79817893312FA69FAFCCBEB29D3E4891
- generatedChecksum: 464372F00208A58A2B6EAFA5A2ABFF66
  logicalPath: config/main/peripheral/adc
  name: plib_adc1.c
  physicalPath: peripheral/adc
  security: NON_SECURE
  type: SOURCE
  userChecksum: 464372F00208A58A2B6EAFA5A2ABFF66
- generatedChecksum: C920DDDEE4B27FD677C128F1A3A3CC39
  logicalPath: config/main/peripheral/can
  name: plib_can0.c
  physicalPath: peripheral/can
  security: NON_SECURE
  type: SOURCE
  userChecksum: C920DDDEE4B27FD677C128F1A3A3CC39
- generatedChecksum: 6C1029525277CDD2766B5818A5EC9517
  logicalPath: config/main/peripheral/clock
  name: plib_clock.c
  physicalPath: peripheral/clock
  security: NON_SECURE
  type: SOURCE
  userChecksum: 6C1029525277CDD2766B5818A5EC9517
- generatedChecksum: 611EE7EB087806C22DEFE7AA240640DA
  logicalPath: config/main/peripheral/dsu
  name: plib_dsu.c
  physicalPath: peripheral/dsu
  security: NON_SECURE
  type: SOURCE
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

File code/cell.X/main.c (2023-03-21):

/**
  Generated Main Source File

  Company:
    Microchip Technology Inc.

  File Name:
    main.c

  Summary:
    This is the main file generated using PIC10 / PIC12 / PIC16 / PIC18 MCUs

  Description:
    This header file provides implementations for driver APIs for all modules selected in the GUI.
    Generation Information :
        Product Revision  :  PIC10 / PIC12 / PIC16 / PIC18 MCUs - 1.81.8
        Device            :  PIC16F1508
        Driver Version    :  2.00
*/

/*
    (c) 2018 Microchip Technology Inc. and its subsidiaries. 
    
    Subject to your compliance with these terms, you may use Microchip software and any 
    derivatives exclusively with Microchip products. It is your responsibility to comply with third party 
    license terms applicable to your use of third party software (including open source software) that 
    may accompany Microchip software.
    
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
    IN NO EVENT WILL MICROCHIP BE LIABLE FOR ANY INDIRECT, SPECIAL, PUNITIVE, 
    INCIDENTAL OR CONSEQUENTIAL LOSS, DAMAGE, COST OR EXPENSE OF ANY KIND 
    WHATSOEVER RELATED TO THE SOFTWARE, HOWEVER CAUSED, EVEN IF MICROCHIP 
    HAS BEEN ADVISED OF THE POSSIBILITY OR THE DAMAGES ARE FORESEEABLE. TO 
    THE FULLEST EXTENT ALLOWED BY LAW, MICROCHIP'S TOTAL LIABILITY ON ALL 
    CLAIMS IN ANY WAY RELATED TO THIS SOFTWARE WILL NOT EXCEED THE AMOUNT 
    OF FEES, IF ANY, THAT YOU HAVE PAID DIRECTLY TO MICROCHIP FOR THIS 
    SOFTWARE.
*/

#include "mcc_generated_files/mcc.h"
#include "mainVars.h"
/*
                         Main application
 */
static void sendAllDatatoMaster();
static void sendDataToMaster(uint16_t);
static void sendVSNSDataToMaster();
static void setDangerSignalLine(bool);
//create structs


struct criticalValues {
    float LOW_VOLTAGE;
    float HIGH_VOLTAGE;
    uint16_t HIGH_TEMP;
    uint16_t WARN_TEMP;
};

struct toTrack {
    uint8_t status;
    uint16_t TSNS1;
    uint16_t TSNS2;
    uint16_t TSNS3;
    uint16_t TSNS4;
    uint16_t TSNS5;
};

//initalize structs to be used in memory
struct toTrack memory = {
    .status = 0x00,
    .TSNS1 = 0x0000,
    .TSNS2 = 0x0000,
    .TSNS3 = 0x0000,
    .TSNS4 = 0x0000,
    .TSNS5 = 0x0000
};
static const struct criticalValues safety = {
    .LOW_VOLTAGE = 3.2,
    .HIGH_VOLTAGE = 4.2,
    .HIGH_TEMP = 226,
    .WARN_TEMP = 230
};
//declare other values to be used in necessary operations

enum ADC_Reference {
    TSNS1 = 0x02,
    TSNS2 = 0x03,
    TSNS3 = 0x07,
    TSNS4 = 0x08,
    TSNS5 = 0x09,
    VSNS = 0x10,
    FVR = 0x1F
} selectedReference;

enum I2C_opCodes {
    No_Command = 0x00,
    Report_TSNS1 = 0x01,
    Report_TSNS2 = 0x02,
    Report_TSNS3 = 0x03,
    Report_TSNS4 = 0x04,
    Report_TSNS5 = 0x05,
    Report_VSNS = 0x06,
    Report_Status = 0x07,
    Enable_Sleep_WDT = 0x08,
    Disable_Sleep_WDT = 0x09,
    Start_Balancing = 0x0A,
    Stop_Balancing = 0x0B,
    Restart_Relay = 0x0C,
    Send_All_Data = 0x0D,
    Controller_Restart = 0x0E
} I2C_Command;

union floatToBytes {
  
    char buffer[4];
    float voltageReading;
  
  } converter;



void main(void)
{
    // initialize the device
    SYSTEM_Initialize();

    // When using interrupts, you need to set the Global and Peripheral Interrupt Enable bits
    // Use the following macros to:

    // Enable the Global Interrupts
    INTERRUPT_GlobalInterruptEnable();

    // Enable the Peripheral Interrupts
    INTERRUPT_PeripheralInterruptEnable();

    // Disable the Global Interrupts
    //INTERRUPT_GlobalInterruptDisable();
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

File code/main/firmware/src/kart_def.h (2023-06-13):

/* 
 * File:   kart_def.h
 * Author: pcguy
 *
 * Created on June 5, 2023, 4:26 PM
 */

#ifndef KART_DEF_H
#define	KART_DEF_H

#ifdef	__cplusplus
extern "C" {
#endif




#ifdef	__cplusplus
}
#endif

#endif	/* KART_DEF_H */

//include defs listed here:
#include "definitions.h"
#include "FreeRTOS.h"
#include "queue.h"



//macro defs listed here:

//cutoffs for kart
#define MINV_LOADED 3.0
#define MINV 3.2
#define HIGHV 4.2
#define HIGH_TEMP 60
#define BALANCE_THRESH 0.0


//basic telemetry info regarding thermistors
#define THERM_COUNT 5
#define CONTROL_VOLT 0x11


//I2C address defs
#define START_ADDRESS 8
#define END_ADDRESS 19
#define TOTAL_REMOTE (END_ADDRESS-START_ADDRESS+1)
#define ARR_ADDR(in) (in-START_ADDRESS)

//macro functions for ease of readability when performing relay checks
#define TEMP_CHECK(in) (in >= HIGH_TEMP)
#define LV_CHECK(in) (in <= MINV_LOADED)
#define LV_RESET(in) (in >= MINV)


//balance check
#define BAL_REQUIRED(in, average) (in >= (average+BALANCE_THRESH))

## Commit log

2022-12-20 Initalized code repo for BMS.
2022-12-21 Engine Block Framework Built
2023-01-06 Full board complete
2023-01-06 Upload New File
    [EV_Kartz_BMS.PrjPcb]
2023-01-27 REPO CHANGE: MCC IS NOW BMS CELL PCB CODE CELL IS DEPRECIATED
    Added in MCC codegen.
2023-02-11 New repos are MCC and Main.
    [configuration.h, pin_configurations.csv]
2023-02-11 Redid some code...
    [BMS Top Cell.PrjPcb, BMS Top Cell.xls, Pg1 Top Sheet and Micro.SchDoc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]
2023-02-11 Added Ultium Files
    [1_wide_cap_pcb_subassm.SLDASM, 1_wide_subassm.SLDASM, 1_wide_subassm_neg.SLDASM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]
2023-02-12 Top Cell_Changes: Added in J_IN and made a couple quick changes.
    [BMS Top Cell.PrjPcb, Pg1 Top Sheet and Micro.SchDoc, Top_Cell.PcbDoc]
2023-02-12 Put my name on my PCB, and avoided plagarism.
2023-02-19 Removed old project files / project codebases that are no longer needed.
    [Top_Cell.step]
2023-03-07 Added in ADC configureation. More work to be done in implementing the equations.
2023-03-10 Implementation is almost done. There is a compile error in main on sendAllDataToMaster. Need to figure it out.
    [main.c]
2023-03-21 I2C [mostly] works
2023-03-25 Added folder for working BMS Code revision
2023-04-04 Returned to I2C mode
2023-04-09 added arduino BMS master controller to version control
2023-04-11 add low pass filter and accumulator on VSNS without resolution increase. More work can be done to account for increased resolution up to 16 bits
2023-04-11 reduced minimum voltage while under load. Relay will not close unless above standard minimum
2023-04-12 Current sensing equation updated to include scaling current offset.
2023-04-12 Added in LED to signify POWER ON.
2023-04-12 Changed pin layout for sam balance 6->5
2023-05-09 recommended change: lowers loaded battery limit based on pdgp data
2023-06-06 Finally got the SAMC working in this instance.
    [configuration.h, pin_configurations.csv]
2023-06-13 Thread basic work ported from Arduino.
